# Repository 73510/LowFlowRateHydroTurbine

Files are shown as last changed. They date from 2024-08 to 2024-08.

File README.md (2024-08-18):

# LowFlowHydroTurbine 🌊⚡

이 저장소는 저유속 수차 연구와 관련된 두 개의 주요 프로젝트를 포함하고 있습니다:

1. [한화 사이언스 챌린지 프로젝트: 저유속 접이식 날개 수차](./HSC2023%20한화%20사이언스%20챌린지/)
2. [KSEF (Korea Science & Engineering Fair) 저유속 수차 연구 프로젝트](./KSEF/)

## 프로젝트 개요 🔍

### 1. 한화 사이언스 챌린지 프로젝트 🏆

이 프로젝트는 저유속 환경에서 효율적으로 작동하는 접이식 날개 수차를 개발하는 것을 목표로 합니다.

주요 구성 요소:
- CFD 분석 데이터 & 코드 💻
  - [CFD automation을 통한 시뮬레이션 과정 효율화](./HSC2023%20한화%20사이언스%20챌린지/Analysis%20Data%20and%20Code/Code%20and%20DXF/CFD%20automation/)
  - [CFD 분석 결과를 통한 토크 최대화](./HSC2023%20한화%20사이언스%20챌린지/Analysis%20Data%20and%20Code/Code%20and%20DXF/Optimize_dxfV1.ipynb)
- 아두이노 코드 🤖
- 설계 파일 (3D 모델링, STL) 🖨️
- 제출 자료 및 문서 📊

[자세한 내용 보기](./HSC2023%20한화%20사이언스%20챌린지/README.md)

### 2. KSEF 저유속 수차 연구 프로젝트 🔬

이 프로젝트는 한화 사이언스 챌린지에서 진행한 연구를 발전시켜 KSEF에 출품한 것입니다.

주요 구성 요소:
- 빌드 파일 (BUILD) 🏗️
- 코드 분석 (Code Analysis) 📊
- 치수 설계 (DIMENSION) 📏
- 문서 (Documentation) 📚

[자세한 내용 보기](./KSEF/README.md)

## 저장소 구조 📂

```
LowFlowHydroTurbine/
├── HSC2023 한화 사이언스 챌린지/
│   ├── Analysis Data and Code/
│   ├── Arduino/
│   ├── 설계/
|   ├── Media/
│   └── 한화 사이언스 챌린지 제출 자료/
└── KSEF/
    ├── BUILD/
    ├── Code Analysis/
    ├── DIMENSION/
    ├── Media/
    └── Documentation/
```

## 주요 기능 및 특징 🌟

- 저유속 환경에 최적화된 수차 설계
- CFD (Computational Fluid Dynamics) 분석을 통한 성능 최적화
- 아두이노를 이용한 실험 환경 제어 및 데이터 수집
- 3D 모델링 및 프로토타입 제작
- 다양한 설계 반복을 통한 성능 개선

## 연구 결과 📈

### 한화 사이언스 챌린지 대상
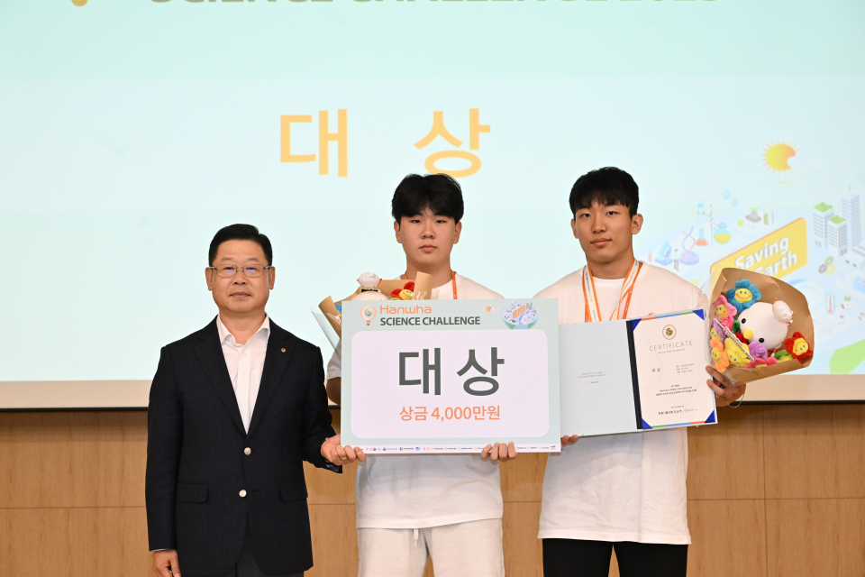
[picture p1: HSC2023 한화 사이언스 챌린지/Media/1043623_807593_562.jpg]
  

  

### KSEF 은상
  
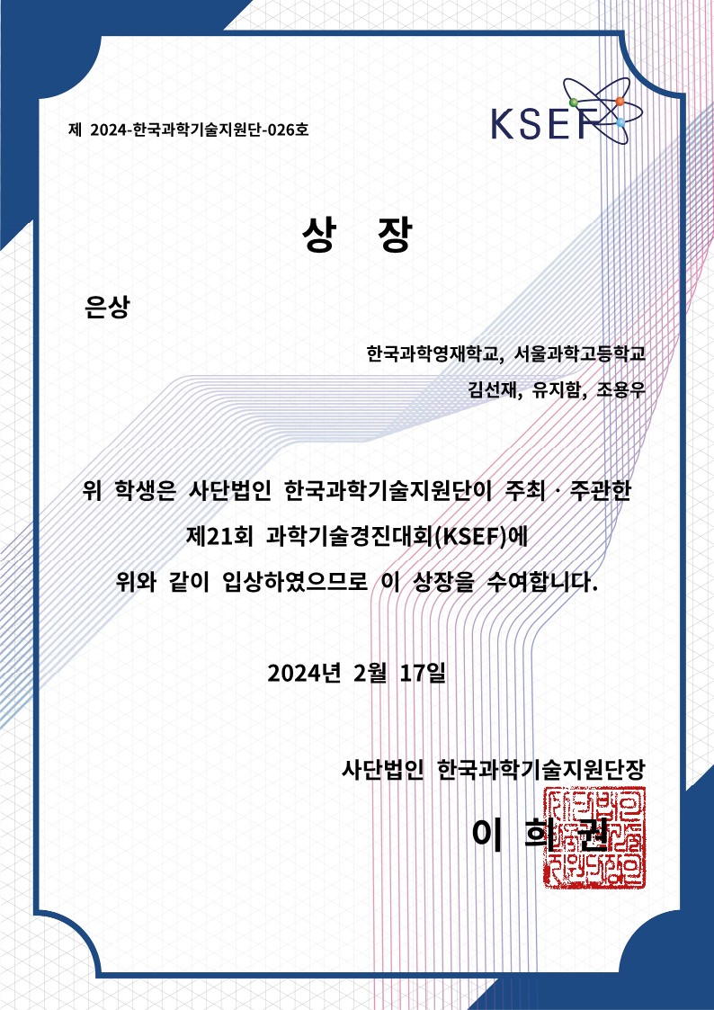
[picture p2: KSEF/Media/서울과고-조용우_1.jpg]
 

 

### 데이터 분석 결과
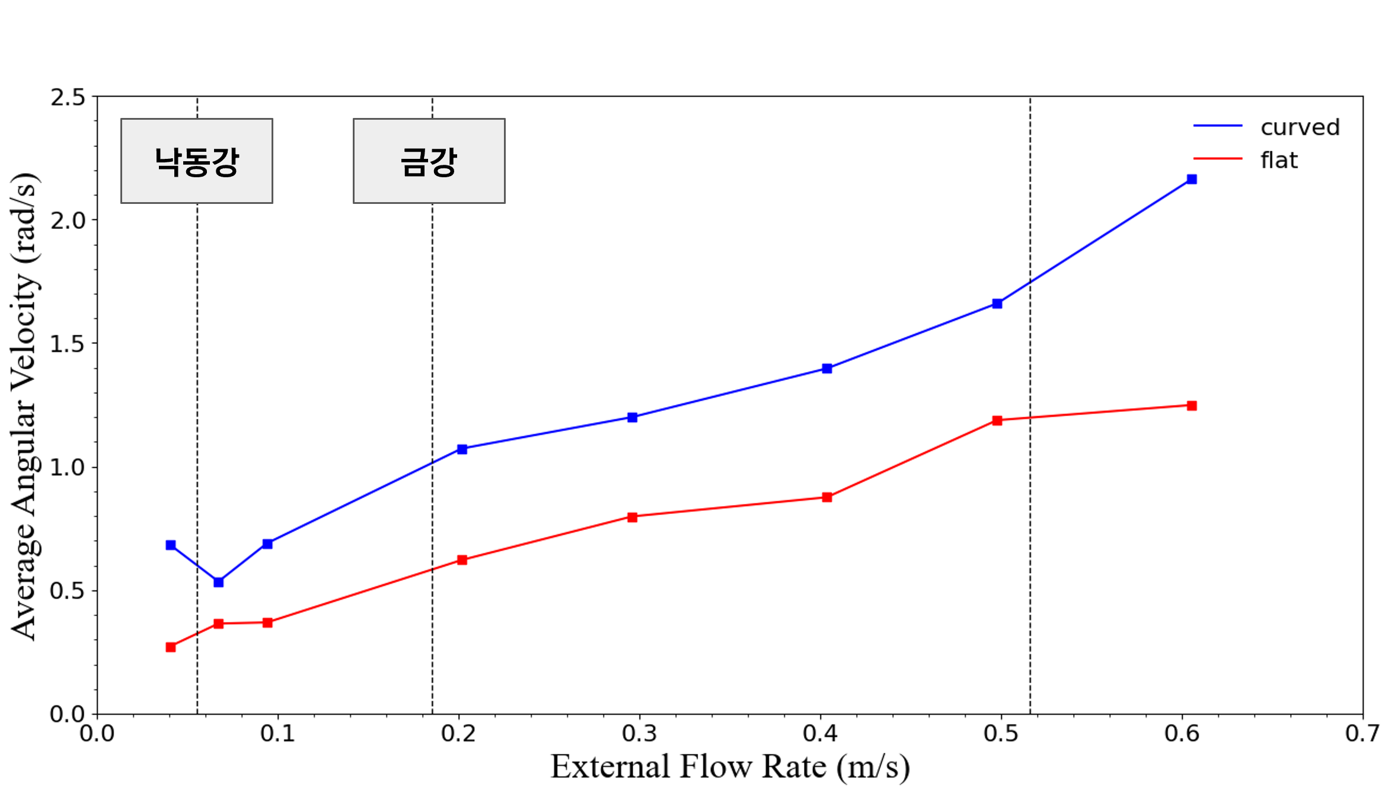
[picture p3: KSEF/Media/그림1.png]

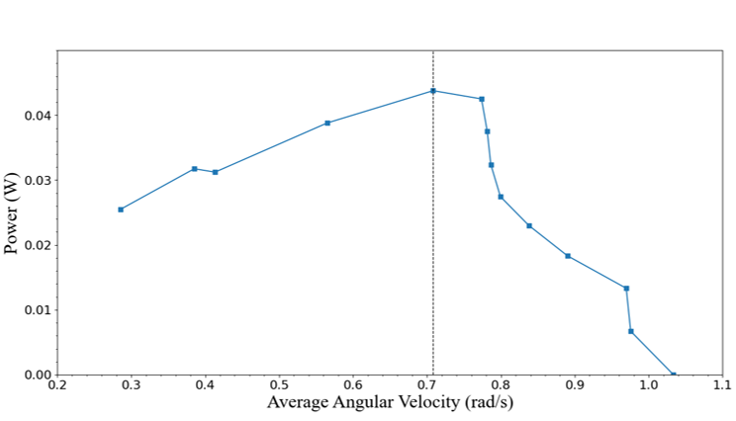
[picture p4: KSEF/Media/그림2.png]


## 기여 및 문의 💌

이 프로젝트에 관심이 있거나 기여하고 싶으신 분들은 언제든지 연락 주시기 바랍니다. 질문이나 제안사항이 있으시면 이슈를 생성하거나 pull request를 보내주세요.

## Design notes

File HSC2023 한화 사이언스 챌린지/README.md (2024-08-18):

# LowFlowHydroTurbine
# 한화 사이언스 챌린지 프로젝트: 저유속 접이식 날개 수차

이 저장소는 한화 사이언스 챌린지에 출품한 저유속 접이식 날개 수차 프로젝트의 모든 자료를 포함하고 있습니다.

## 목차

1. [CFD 분석 데이터 (CFD Analysis Data)](#분석-데이터)
2. [아두이노 코드 (Arduino)](#아두이노-코드)
3. [설계 파일 (Design Files)](#설계-파일)
4. [한화 사이언스 챌린지 제출 자료 (Files submitted to Hanwha Science Challenge)](#한화-사이언스-챌린지-제출-자료)

## [CFD 분석 데이터](./Analysis%20Data%20and%20Code/)

Computational Fluid Dynamics (CFD) 분석 및 최적화 관련 파일들이 이 섹션에 포함되어 있습니다.
[**Code and DXF**](./Analysis%20Data%20and%20Code/Code%20and%20DXF/)
- optimize_dxfV1
  - 수차의 CFD 결과 기반 토크 계산 및 최적화
  - 최적화 이후 Smoothing 코드
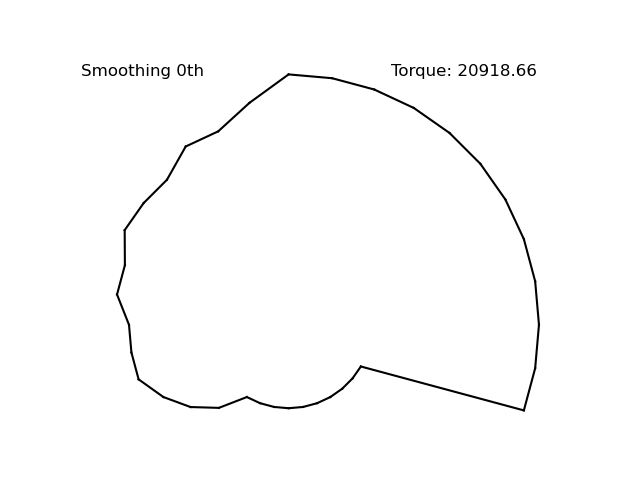
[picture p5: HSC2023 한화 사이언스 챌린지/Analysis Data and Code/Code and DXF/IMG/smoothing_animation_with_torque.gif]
  
  - 분석 기반 DXF (Angleblock 단면 형상) 제작 코드
- full, half, straight, straightWF : 각 날개의 최적화 DXF 형상

- [**CFD automation**](./Analysis%20Data%20and%20Code/Code%20and%20DXF/CFD%20automation/)
  - 0~360도까지, 10도 단위로 유속과 날개가 이루는 각을 바꾸어가며 날개가 받는 힘을 측정하는 코드. 
  - 이 과정에서, 반복되는 작업을 pyautogui로 자동화하여 효율화시켰습니다.
  - [fullauto.py](./Analysis%20Data%20and%20Code/Code%20and%20DXF/CFD%20automation/fullauto.py) : 완전히 자동화 시켜 0~360도까지 반복하며 데이터를 기록
  - 이로써 36*4 = 144개의 CFD 데이터를 일관되게 얻었습니다.
  - 작동 영상

코드 실행부터 CFD 실행까지



CFD 실행 이후, 벽 계산기로 토크를 계산하는 과정 자동화



## [아두이노 코드](./Arduino/)

실험 환경 제어 및 데이터 수집을 위한 아두이노 코드가 이 섹션에 있습니다.
- [어항 내 물의 흐름을 제어하는 코드 (단순 속도)](./Arduino/Motor_Control_SpeedControlOnly)
- [어항 내 물의 흐름을 제어하며 유속과 수차의 회전 속도를 IR 센서로 측정하는 코드](./Arduino/Motor_Control_SpeedControlandTachometer)

## [설계 파일](./설계/)

수차와 관련 부품들의 3D 모델링 파일 및 설계도면이 이 섹션에 있습니다.

- [STL](./설계/STL/) : 수차를 설계한 STL 파일을 모았습니다.
- [어항 설계](./설계/어항%20설계/) : 어항 구조물을 설치하는데 사용한 설계 파일입니다.
- Acryl Wall Arduino Placement : 아두이노를 설치하기 위해 만든 아크릴 판 구조물입니다.
- Acryl Wall : 아크릴 벽으로 어항 내부의 흐름을 나누어 순환하게 했습니다.

## [한화 사이언스 챌린지 제출 자료](./한화%20사이언스%20챌린지%20제출%20자료/)

프로젝트 관련 모든 문서 파일들이 이 섹션에 포함되어 있습니다:

- 아이디어 발표 자료
- 토론 발표 자료
- 한사챌 보고서
- 기존 연구 결과 자료
- 결과 전시물 계획서
- 판넬사진 출력 파일
- 기존 연구 특허출원번호 10-2010-0027024 수정 날개 접이식 수차 자료

이 문서들은 프로젝트의 전체적인 진행 과정, 연구 결과, 및 최종 제출 자료들을 포함하고 있습니다.

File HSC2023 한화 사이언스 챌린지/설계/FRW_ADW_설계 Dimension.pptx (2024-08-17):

## HSC2023 피쉬파워

## 설계 Dimesion Documentation

- 회전부는 0.7mm 여분 (지름기준), 고정부는 0.2mm 여분 (지름 기준)
- -> 이거 한번 싹다 검토하고 맞추기

## 베어링이 필요한가?

- 추가적인 무게
- 감소하는 저항
- 증가하는 안정성
- 불필요한 이동의 제한
- 부품 수의 증가, 조립 시간 길어짐, 파손 우려 높아짐

## 어떤 봉을 쓸 것인가

6mm환봉
6mm 4mm 파이프는 파손될 우려가 있어 약간 보강한다.

## 어항

- 일단 어항 자체는 측정이 필요.
사용 어항 링크 (https://www.coupang.com/vp/products/4395243507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)

## 어항 profile & 실험장치

Aluminum Profile 20 * 20 필요한 것 :
424 * 3
110 * 2
100 * 1
585 * 2
290 * 3
145 * 1
이거만 있으면 됨.

3D printed parts :
3D motor mount
Barmount 0,1
Barmount 3

## 어항 profile 실험장치의 주요 settings

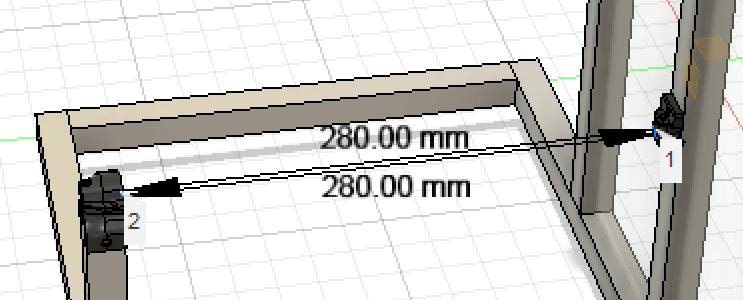
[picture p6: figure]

RotorBar Length : 290

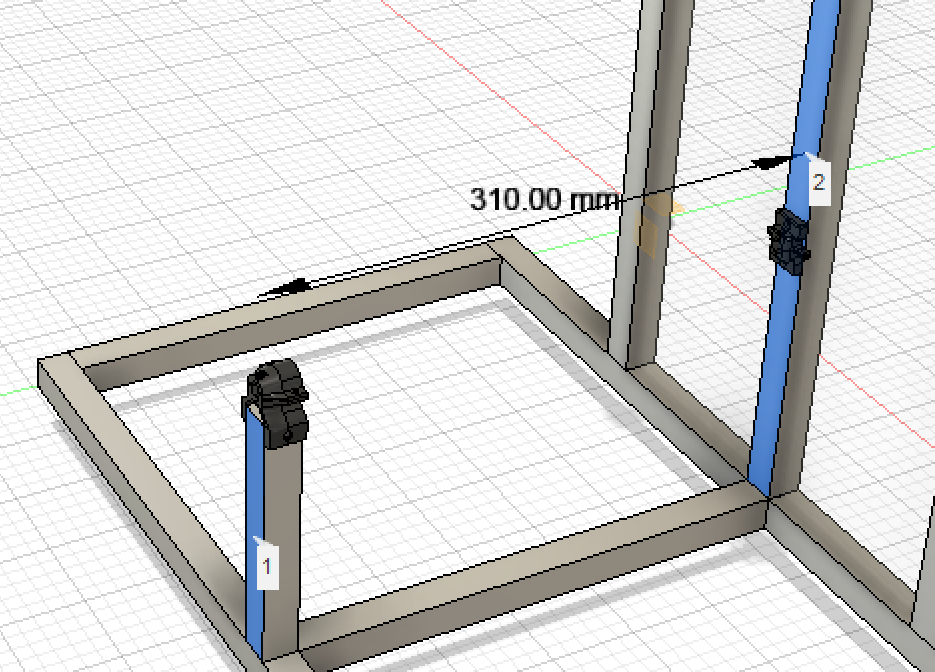
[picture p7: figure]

Rotor Parts Length : 290-30 = 260mm
Barmount 01이 10mm
Barmount 3이 20mm 먹음
둘 다 끝단에서 5mm 떨어진 중심에서 3mm 빵꾸 내놓음.
필요 고정 나사 : 16~20mm
RotorBar는 고정되어있음.

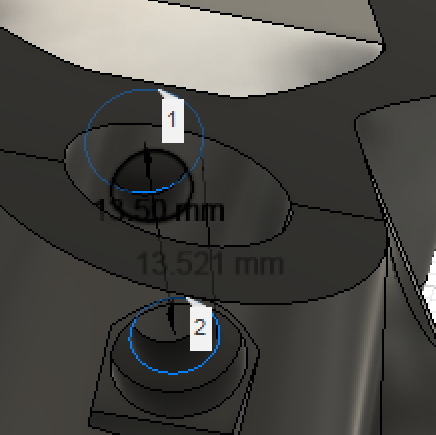
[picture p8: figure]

## 자유회전 물레방아 (FRW)

- Free Rotating Wheel

## FRW, 축 정의

B center rotational axis / B 중심 회전축 -> B-CRA

B Flap rotational axis / B 날개 회전축 -> B-FRA

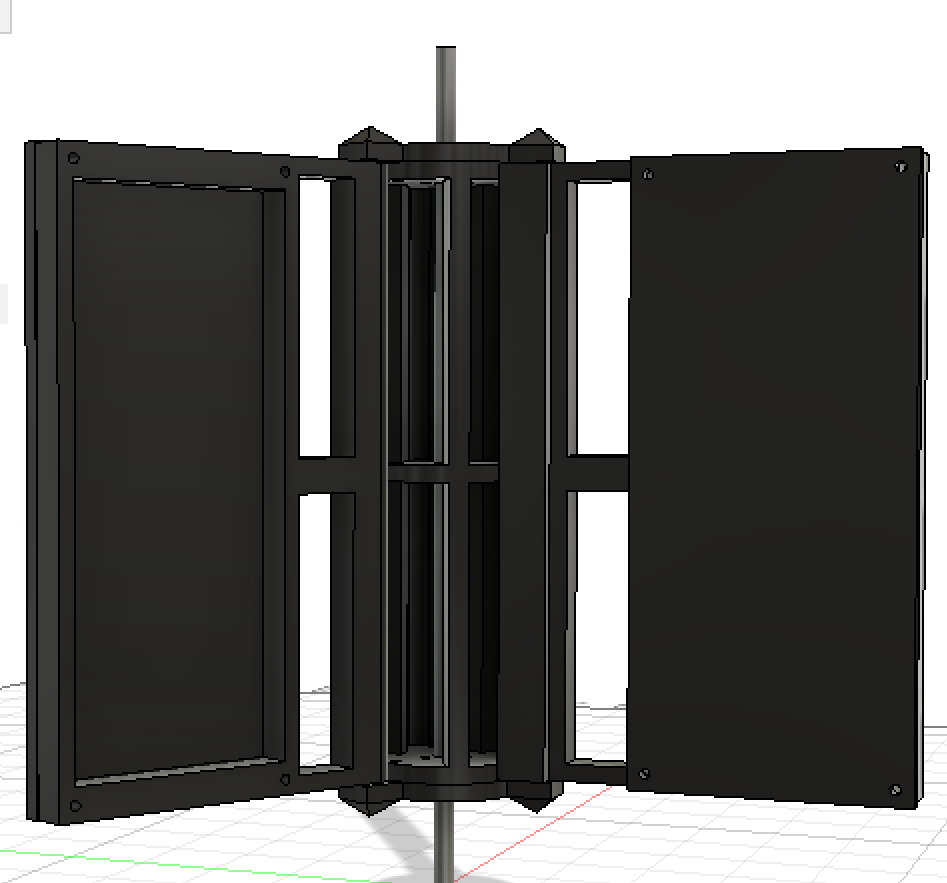
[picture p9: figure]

B : Bar

## FRW : Axial dimesion

gearAT : axial thickness of gear 기어의 축방향 두께
FlapcapAT : axial thickness of gear / Flapcap의 축방향 두께
FlapAT : axial thickness of flap / Flap의 축방향 두께
S1 : space between flapcap(L, R) and flap / flapcap 과 flap 사이의 여분 공간
CenterPieceAT : axial thickness of CenterPiece / CenterPiece 의 축방향 두께
S2 : space between gear and barmount / gear와 barmount 사이의 두께
S3 : space between FlapcapR & barmount
Black : Rotating Parts, Drilled on to B-CRA (rotates with B-CRA)
Blue : not rotating Parts, connected to B-CRA via Bearing
S : spaces (needs to be bigger than 1mm)

Barmount
01

S2

gearAT

flapcapAT
(L)

S1

FlapAT

CenterPieceAT

S1

flapcapAT
(R)

S3

Barmount
3

## FRW Radial Dimension

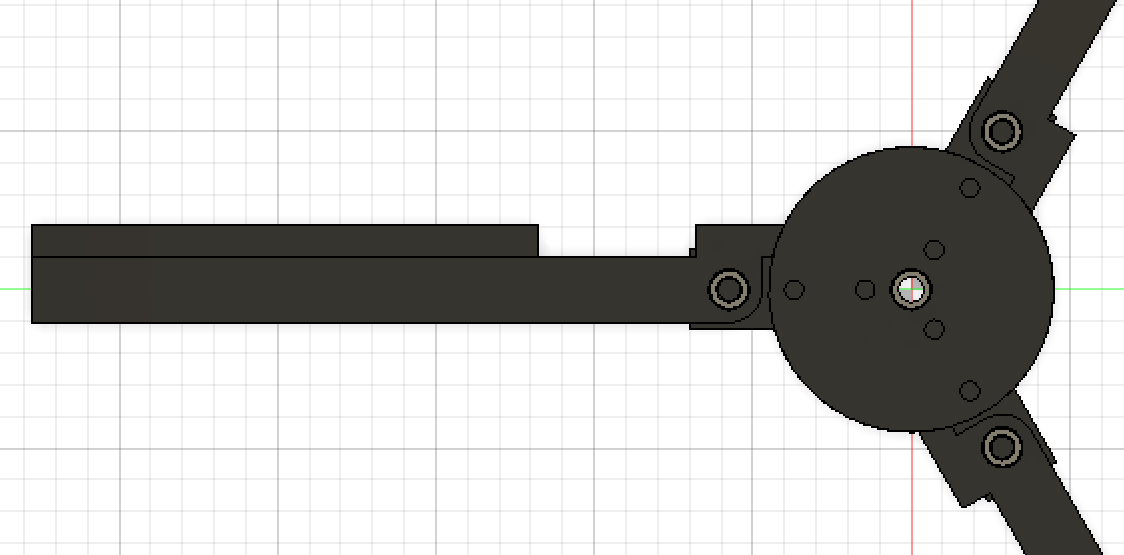
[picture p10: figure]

FF-RT = 90
(Flap Frame Radial Thickness)

F-RT = 80
(Flap Radial Thickness)

B-CRA to B-FRA = 60

## FRW – constraints for build

Barmount
01

S2

gearAT

flapcapAT
(L)

S1

FlapAT

CenterPieceAT

S1

flapcapAT
(R)

S3

Barmount
3

s2+ gearAT + 2*flapcapAT + CenterPieceAT + s3 = 280mm
2s1 + flapAT = CenterPieceAT
gearAT >= 10, flapcapAT >=10
S >=2
+ flapAT = flapAT(camversion, cyclodialversion)

## FRW – Axial/Radial 수치

Axial 수치
gearAT = 16mm
Total -> 2*2 + 16 + 10*2 + 124 = 164mm
중심에서 24mm 떨어뜨려서 배치필요.

Radial 수치
FF-RT = 90
F-RT = 80
B-CRA to B-FRA = 60
G to FC mount = 10
FC to CB mount = 40
CB roller = 50

## ADW/ 각도 정의 물레방아

- Angle Defined 물레방아

## ADW, 축 정의

B center rotational axis / B 중심 회전축 -> B-CRA

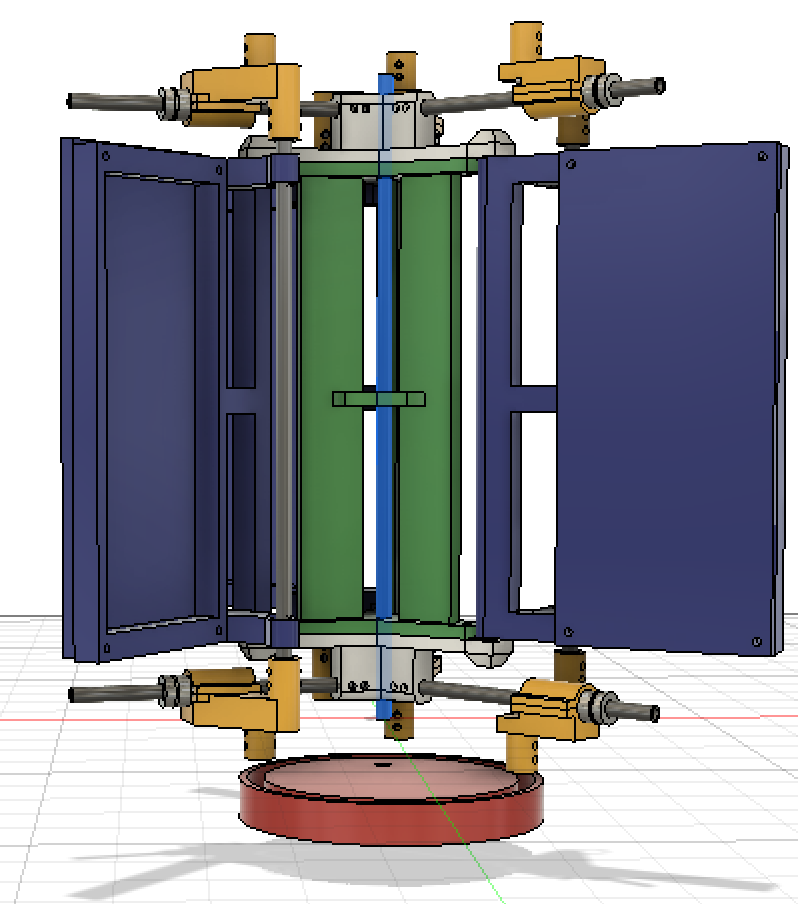
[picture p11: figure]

B Flap rotational axis / B 날개 회전축 -> B-FRA

B Flap pin slot/ B 날개 각도축 -> B-FPS

B Angle Linear Axis / B 각도선형축 -> B-ALA

B Angle rod -> B-AR

B : Bar

## ADW 부품 정의

CB - CenterBody / 중심체

FF - Flap frame / 날개 뼈대

F - Flap / 날개

FC - FlapCap / 날개 뚜껑

LAG - Linear Angle guide / 선형 캠 가이드

AB - AngleBlock / 각도블럭

## ADW LAG (linear angle guide) dimension

1. Tangent to radial vector

B-FPS fix

LAG main body / LAG-MB

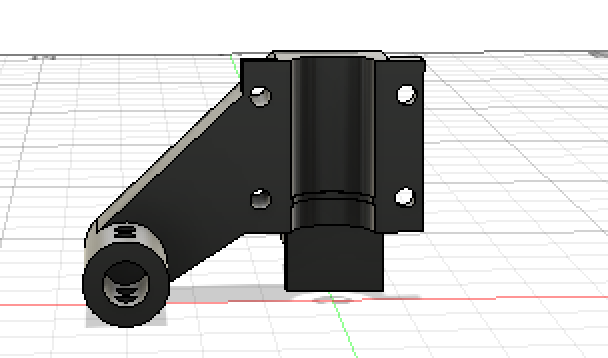
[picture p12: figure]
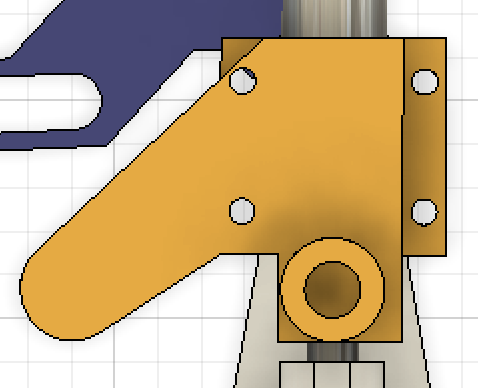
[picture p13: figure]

B-AR fix

LAG leftover

Δy

LAG bearing holder / LAG_BH

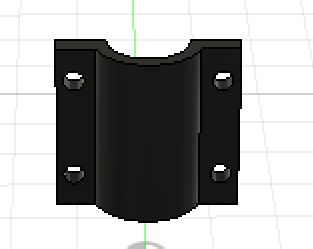
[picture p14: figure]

d

현재 설계에서 d = 30mm, Δy = 0mm

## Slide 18

ADW LAG_L (linear angle guide) dimension

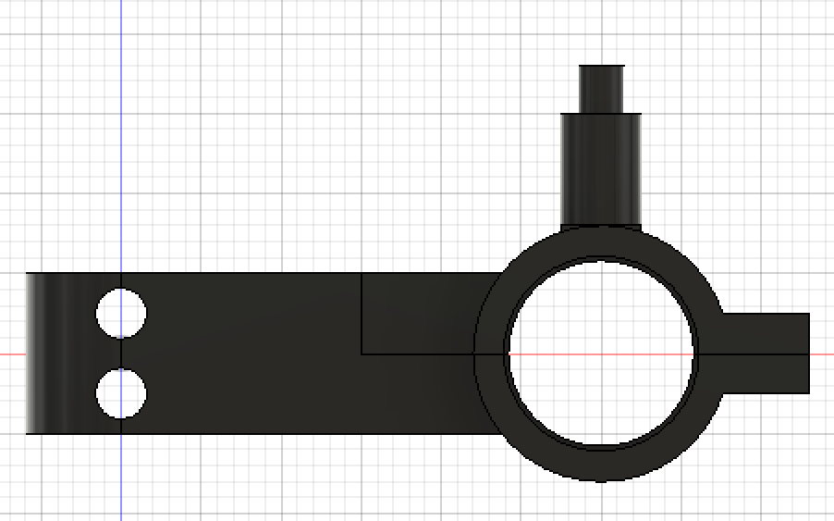
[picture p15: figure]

BFL : Bar Fix Length
FT : FixingThickness
LAG-B-AT : LAG Body Axial thickness
Bearing Diameter = 12mm
B-ALA to BearingMount = 15mm
Bearing type = 683zz

FT

BFL

## ADW LAG

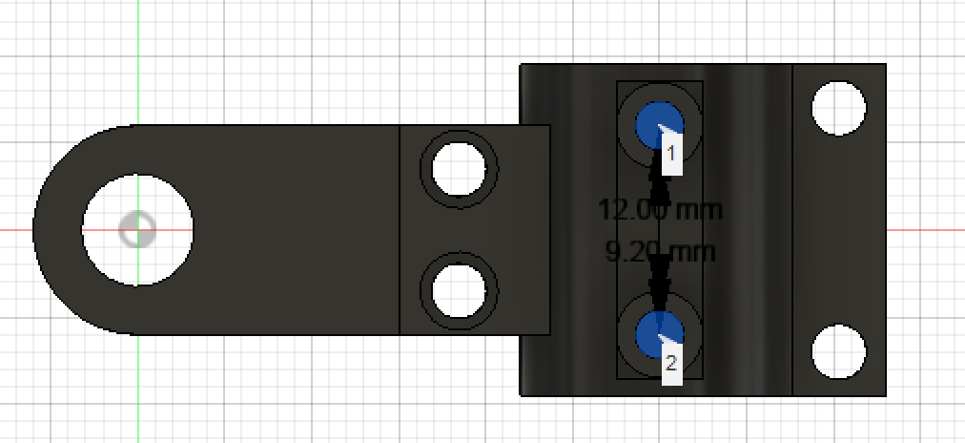
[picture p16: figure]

Angle Block 두께

distance of bearings (center) = 12mm
Bearing radius : 3.5mm
AB 두께 : 5mm, 여분 고려하여 4.5mm로 함. 별도의 베어링 고정은 없으며 필요시 글루건/순접으로 할 것

## ADW LAG dimensions

BFL : 10mm
FT : 1.8mm
LAG-B-AT : LAG Body Axial thickness
Bearing Diameter = 12mm
베어링 고정부 Diameter = (실제 고정시 편의를 위해 여분) ->6.1*2

## ADW Flapcap dimension

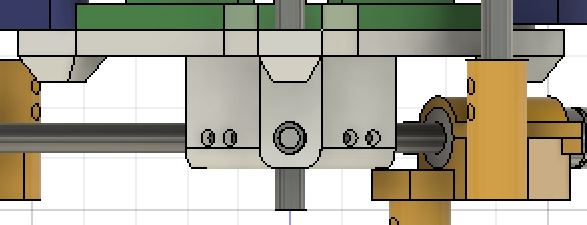
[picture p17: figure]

B-ALA-S : B-ALA spacing

Bar Margin

## ADW Axial Dimension

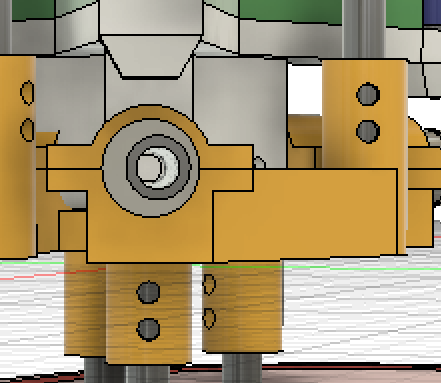
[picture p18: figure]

AB-AT : Angle Block Axial Thickness, 각도블럭 axial 두께
FC-AT : Flap Cap Axial Thickness, flapcap 축방향 두께
G-AT : Gear Axial Thickness, 기어 축방향두께
LAG-AT : Linear Angle Guide Axial Thickness
BFL : Bar Fix Length
LBT : Linear Bush Thickness
LAG-LB-B-T : LAG linear bearing body thickness
LAG-B-AT : LAG Body Axial thickness

Barmount
01

S

G-AT

S

AB-AT

S

BFL

LAG-B-AT

BFL

LAG-BH-AT

S1

FlapAT

CenterPieceAT

S1

BFL

LAG-BH-AT

LAG-B-AT

BFL

S

AB-AT

S

Barmount
3

B-ALA-S

B-ALA-S

## ADW

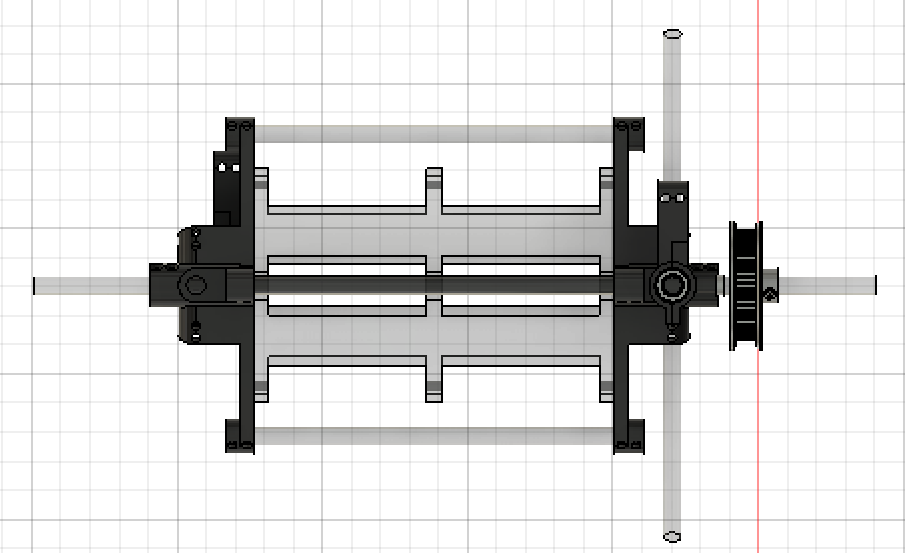
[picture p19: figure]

## ADW Radial Dimension

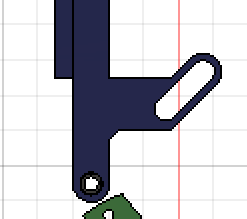
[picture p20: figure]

B-CRA to B-FRA

(2)^0.5 *d

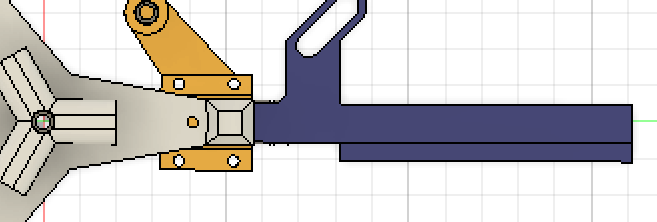
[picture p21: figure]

d

F-RT (Flap Radial Thickness)

B-ALA Fix

## ADW 0~90이 나오기 위한 Angle Block

When 45deg Flap Attached, Radial Value of Angle Block

0deg = (B-CRA to B-FRA) – d + Δy = 60-30 = 30
LAG는 중심에서 10정도 떨어져 있음
Bar Fix는 중심에서 20까지만 있어야 함.
90deg = (B-CRA to B-FRA) + d + Δy = 60+30 = 90
B-ALA 는 20~ 100까지 필요.
따라서 필요길이는 80, 고정부 15로 계산하여 길이 95임

## Constraints of ADW

Barmount
01

S

G-AT

S

AB-AT

S

BFL

LAG-B-AT

BFL

LAG-BH-AT

S1

FlapAT

CenterPieceAT

S1

BFL

LAG-BH-AT

LAG-B-AT

BFL

S

AB-AT

S

Barmount
3

B-ALA-S

B-ALA-S

5*S + G-AT + 2*(AB-AT + BFL + LAG-B-AT + B-ALA-S) + CenterPieceAT <= 280mm
S >= 2mm
2*S + FlapAT = CenterPieceAT
(B-CRA to B-FRA) – d - LAG leftover >= B-ALA Fix
(B-CRA to B-FRA) + F-RT <= 150
FlapAT (ADW, FRW, CPW)

## ADW parametrics

Axial 수치
S = 2
gearAT = 16mm
flapcap = 36mm
Flap = 120
CenterPieceAT = 124
BFL = 10
LAB-B-AT = 5
B-ALA-S = 10

LAG 수치
D = 30
Δy = 0 (하지만 d를 늘릴경우 증가 시켜야 함)

Radial 수치
FF-RT = 90
F-RT = 80
B-CRA to B-FRA = 60
G to FC mount = 10
FC to CB mount = 40
CB roller = 50

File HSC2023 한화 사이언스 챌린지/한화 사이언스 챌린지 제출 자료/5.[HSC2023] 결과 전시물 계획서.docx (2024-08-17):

전시 결과물 계획서

[계획서 작성 안내]

- 조형물의 규격 및 특이사항을 명기하고, 사진자료를 첨부하여 1매 이내로 작성하여, 타 연구자료와 함께 제출하여 주시기 바랍니다.

- 운영위원회 결정에 따라 결과물 전시가 제한될 수 있습니다.
(안전, 위험성 등 고려)

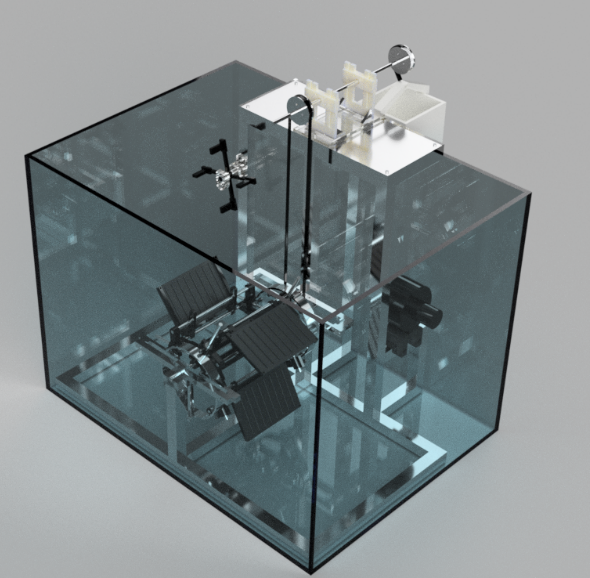
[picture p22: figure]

60 x 45 x 45cm 어항 + 실험장치입니다. 물을 넣어야 해서 바퀴 달린 수레 위에 올려놓고 사용하고자 합니다. 저희 집에서 사용할 정도로 안전합니다.

수레 위에 올려놓고 사용하면 130 * 80 * 80 cm 일 것으로 예상됩니다.

프로젝트명 | 저유속에서 발전가능한 접이식 날개 수차
팀명 | 피쉬 파워
지도교사 성명 | 배동일
팀원 성명 | 1. 조용우 | 2. 서동주

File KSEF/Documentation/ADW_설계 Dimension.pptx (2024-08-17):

## ISEF_ADW

## 베어링이 필요한가?

베어링 종류 – 682OP
외경 5, 내경 2, 두께 1.5
ADW FF에는 베어링 없이 함.

## 어떤 봉을 쓸 것인가

외경6mm 내경 4mm 파이프
2mm 카본 로드

## ADW, 축 정의

B center rotational axis / B 중심 회전축 -> B-CRA


B Flap rotational axis / B 날개 회전축 -> B-FRA

B Flap pin slot/ B 날개 각도축 -> B-FPS

B Angle Linear Axis / B 각도선형축 -> B-ALA

B Angle rod -> B-AR

B : Bar

## ADW 부품 정의

CB - CenterBody / 중심체

FF - Flap frame / 날개 뼈대

F - Flap / 날개

FC - FlapCap / 날개 뚜껑

LAG - Linear Angle guide / 선형 캠 가이드

AB - AngleBlock / 각도블럭

## ADW Axial Dimension


AB-AT : Angle Block Axial Thickness, 각도블럭 axial 두께
FC-AT : Flap Cap Axial Thickness, flapcap 축방향 두께
G-AT : Gear Axial Thickness, 기어 축방향두께
LAG-AT : Linear Angle Guide Axial Thickness
BFL : Bar Fix Length
LBT : Linear Bush Thickness
LAG-LB-B-T : LAG linear bearing body thickness
LAG-B-AT : LAG Body Axial thickness

Barmount
01

S

G-AT

S

AB-AT

Linear Bearing Casing Diameter

FlapCap

FlapCap

Linear Bearing Casing Diameter

AB-AT

Barmount
3

LAGAB

Til B-ALA

B-ALA-S

S1

FlapAT

CenterPieceAT

S1

Til B-ALA

B-ALA-S

## ADW Radial Dimension


B-CRA to B-FRA

(2)^0.5 *d


d

F-RT (Flap Radial Thickness)

B-ALA Fix

## Constraints of ADW

G-AT

Barmount
01

AB-AT

Linear Bearing Casing Diameter

FlapCap

FlapCap

Linear Bearing Casing Diameter

AB-AT

Barmount
3

LAGAB

Linear Bearing Casing Diameter

B-ALA-S

S1

FlapAT

CenterPieceAT

S1

B-ALA-S

Barmount01 10mm
S = 2
G-AT = 10
AB-AT = 20
LAGAB_ = 20
Linear Bearing Casing Diameter = 8
B-ALA-S = 10
FlapCap = 5

S

S

S

Linear Bearing Casing Diameter

## ADW parametrics

Axial 수치
Barmount01 10mm
S = 2
G-AT = 10
AB-AT = 20
LAGAB_ = 20
Linear Bearing Casing Diameter = 8
B-ALA-S = 10
FlapCap = 5

LAG 수치
D = 20
Δy = 19/2 (하지만 d를 늘릴경우 증가 시켜야 함)

Radial 수치
FF-RT = 50
F-RT = 45
B-CRA to B-FRA = 40
40+20+19/2+20 = 90
110-8

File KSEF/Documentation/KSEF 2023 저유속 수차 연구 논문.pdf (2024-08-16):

제21회 KSEF과학프로젝트대회

- 1 -

### 1. Introduction

친환경적이면서 동시에 유의미한 발전을 할 수 있는 에너지 하베스팅 방식은 흔하지 않다. 현존하는 수력 발전 시스템은 빠 른 유속을 요구하거나, 큰 수위 차를 요구하는데, 해당 두 조건 이 만족되지 않는 환경에서는 인위적으로 댐을 설치하여 수력 발전을 가능케 하기도 한다. 이러한 기존 수력 발전 시스템은 환경적인 면에서 좋지 않다는 평가를 받고 있다.
물레방아는 댐과 같은 수력 발전 방식과 비교했을 때 24시간 발전이 가능하고, 비교적 친환경적이라는 큰 장점을 가지고 있 다. 다만 기존의 물레방아는 그 구조와 관계없이, 반드시 일부 분이 물에 잠겨야만 한다는 단점을 지니고 있다. 그림 1에 나 타난 대표적인 형태의 물레방아들 모두 물의 흐름이 균일할 때 일부분이 잠겨서 토크를 얻는 방식을 이용하고 있다.

[Fig. 1] 물레방아의 회전 원리, 왼쪽부터 Undershot water wheel, applied for watermilling since the 1st century BC / Overshot water wheel, applied for watermilling since the 1st century BC / Breastshot water wheel, applied for watermilling since the 3rd century AD

따라서 기존의 물레방아는, 물레방아가 물에 전부 다 잠긴 상 황에서는 돌림힘이 작용하지 않아 에너지를 생산할 수 없다는 큰 단점을 지닌다. 이는 물레방아의 설치를 어렵게 하고, 환경 적 변수가 발생했을 시 수선이 까다로우며, 조경을 해치는 원인 이 된다. 본 연구에서는 물레방아에 캠 구조와 수동적 날개 조 정 시스템을 적용해, 물에 전부 다 잠긴 상태에서도 에너지 생

## 수동적 날개 조정을 위한 캠 구조 적용 수중 물레방아의 설계 및 제작

김선재¹

, 유지함¹

, 조용우²
1한국과학기술원 부설 한국과학영재학교,

2서울과학고등학교

## Design and Development of an Underwater Watermill with Cam Orientation for Passive Blade Pitching System

Sunjae Kim¹

, Jihahm Yoo¹

, Yongwoo Cho²
1Korea Science Academy of KAIST, Busan, Korea 2Seoul Science High School, Seoul, Korea

요 약 캠 구조와 수동적 날개 조정 시스템을 이용한 물레방아는 물 안에 전부 잠겨도 돌림힘이 작용해 에너지를 생산할 수 있다. 본 연구에서는 캠 구조와 수동적 날개 조정 시스템이 적용된 물레방아의 에너지 생산량과 기존 방식 대비의 환경적 이득을 탐구하였다. 먼저 간단화 시뮬레이션을 통해 본 연구의 물레방아가 수중에서 회전할 수 있음을 검증하였고, Fusion 360 프로그램을 통해 모델링하였다. 이후 초기 버전으로 3-Flat Version을 제 작한 후, 날개 수와 날개 모양을 수정해 최종적으로 4-Flat Version과 4-Curved Version의 두 물레방아를 제작하였다. 제작된 두 물레방아를 Endless Pool과 직접 제작한 실험 환경에서 실험해 외부 유속 vs. 평균 각속도 vs. Power 데이터를 획득한 결과, 본 연구의 물레방아가 기존 물레방 아가 발전하지 못하던 환경에서도 큰 수준의 에너지를 생산할 수 있음을 확인할 수 있었으며, 현재 수중 에너지 발전 방식으로 많이 이용되고 있는 Underwater Windmill과 비교해도, 본 연구의 물레방아가 환경적인 측면에서 큰 이점을 가짐을 검증하였다. 향후 연구에서 본 장치의 마찰 최소화(자 기 부상), 캠 구조의 개선, 그리고 대형화를 통해 본 연구의 물레방아의 발전량을 유의미하게 증가시킬 수 있을 것으로 기대한다.

Abstract The waterwheel equipped with a cam structure and a passive wing adjustment system can produce energy even when fully submerged in water due to the action of rotational force. In this study, the energy production of the waterwheel equipped with the cam structure and passive wing adjustment system was investigated, along with the environmental benefits compared to conventional methods. Initially, the waterwheel's ability to rotate underwater was verified through simplified simulations, and the model was designed using Fusion 360 software. Subsequently, an initial version, the 3-Flat Version, was fabricated and further modified in terms of the number and shape of the wings. Finally, two waterwheel versions, the 4-Flat Version and the 4-Curved Version, were produced. Experiments were conducted using the fabricated waterwheels in an Endless Pool and a testbed constructed at the school to acquire data on external flow rate vs. average angular velocity vs. power. The results revealed that the waterwheel in this study could produce a substantial amount of energy even in environments where conventional waterwheels could not, and when compared to the widely used underwater windmill for underwater energy generation, it exhibited significant environmental advantages. Future research is expected to focus on minimizing friction (magnetic levitation), improving the cam structure, and scaling up the device, aiming to significantly increase the waterwheel's power generation capacity. Key Words : Underwater Watermill, Cam, Passive Blade Pitching System, Energy Harvesting

- 2 -

산을 가능하게 하여 기존 물레방아의 단점을 해결하고, 친환경 적이면서 효과적인 수중 에너지 발전 방식을 제시하고자 한다.

### 2. Background Study

2.1 기존 접이식 날개를 이용한 수력 발전 모델

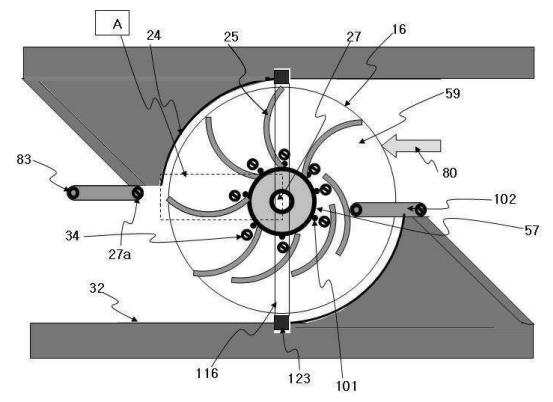
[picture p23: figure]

[Fig. 2] 대한민국 특허청에 등록된 특허 10-2010-0027024, 접이식 날개 수차

위의 접이식 날개를 이용한 수력 발전 모델은 유도판 을 사용하여 날개를 접어 토크의 차이를 발생시켜 발전 을 하는 방식이다. 해당 모델은 날개들이 유도판에 충 돌을 하면서 날개가 접히는 방식으로 설계를 하였다. 양쪽에 설치된 유도판은 복류식으로 발전이 가능하도록 설계되었고, 저 유속, 저 낙차에서도 높은 효율로 발전 할 수 있도록 설계되었다.

2.2 펠톤 터빈

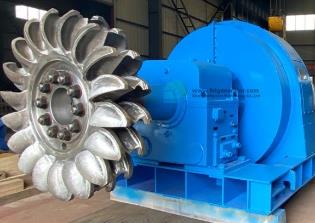
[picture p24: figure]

[Fig. 3] 펠톤 터빈

펠톤 터빈은 물을 노즐로부터 분출시켜 위치 에너지 를 운동에너지로 바꾸는 수차로 충돌형 수차이다. 수압 에 의해 버킷에 부딪히는 물의 힘으로 회전력을 발생시 킨다. 유량을 조정할 수 있는 기구를 갖추고 있고, 유량 조정이 최우선 되는 경우에 사용할 수 있다. 펠톤 수차 는 단류식 수차이다.

2.3 캠 샤프트 구조(Cam Shaft Structure)

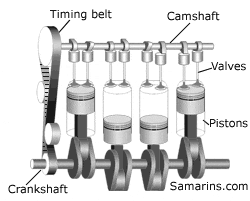
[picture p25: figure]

[Fig. 4] Cam Shaft 구조

캠 샤프트는 내부 연소 엔진의 작동을 제어하는 중요 한 부품 중 하나로, 밸브의 개방과 폐쇄를 조절하여 연 소 과정을 조절한다. 카메라 샤프트는 엔진 블록 내부 에 위치하며, 엔진의 크랭크 샤프트와 동기화하여 작동 한다.

캠 샤프트는 여러 개의 커브 또는 로브로 구성되어 있으며, 이 커브들은 밸브의 개방과 폐쇄 시기를 결정 한다. 엔진 작동 시, 크랭크 샤프트의 회전과 함께 카메 라 샤프트도 회전하게 되며, 각 로브의 모양과 크기에 따라 밸브가 열리고 닫히는 타이밍이 결정된다.

캠 샤프트는 크게 흡기 밸브와 배기 밸브의 작동을 제어하는 두 가지 유형으로 나뉜다. 인테이크 샤프트는 연료와 공기가 실린더 내부로 흡입되는 과정을 제어하 며, 익스테이크 샤프트는 연소 후 배기 가스가 실린더 에서 배출되는 과정을 제어한다.

2.4 수동적 날개 조정을 위한 캠 구조 적용 수중 물 레방아의 회전 원리

본 연구에서 제작한 수동적 날개 조정을 위한 캠 구 조 적용 수중 물레방아는 2.1의 접이식 날개와 2.3의 캠 샤프트 구조를 중심적으로 이용한다. 기울어진 날개 들을 통해 균일한 유속에서도 토크를 발생시키는 것이 본 연구의 물레방아의 기본 원리인데, 캠 구조를 통해 날개가 기울어지는 각도를 자유자재로 제어하여 이를 실현하였다.

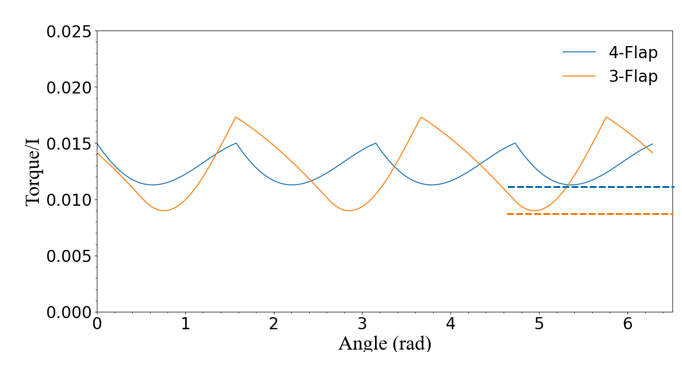
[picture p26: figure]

- 3 -

### 3. 간단화 시뮬레이션

3.1 토크 방정식 유도

본 절에서는 수동적 날개 조정을 위한 캠 구조 적용 수중 물레방아의 적용 가능성을 간단화 시뮬레이션을 통해 확인하고자 한다.

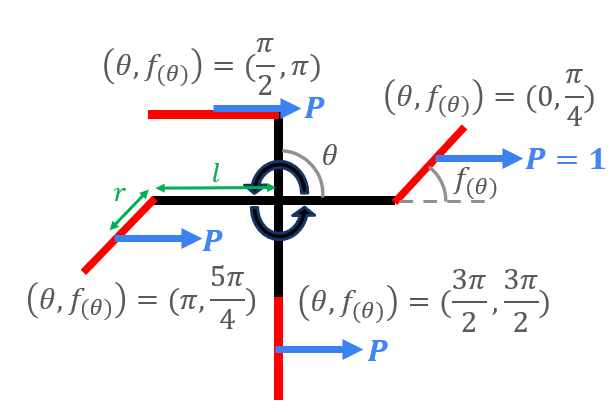
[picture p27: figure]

[Fig. 4] 간단화 시뮬레이션, 물레방아 구조와 상황

위 그림 4는 물이 왼쪽에서 오른쪽으로 흐르는 상황 에서의 물레방아 상황을 나타낸 그림이다. 원래 물의 흐름을 고려해 각 날개에 작용하는 힘의 크기를 구해야 하지만, 본 간단화 시뮬레이션에서는 각 날개에 크기 1 의 압력이 중심에 균일하게 작용한다고 가정한다. 이때 물레방아와 날개를 잇는 부분의 각도를 θ라 정의하고, 날개의 각도를 f(θ)라 정의하자. θ의 범위에 따른 f(θ)의 크기는 아래의 수식을 만족한다.

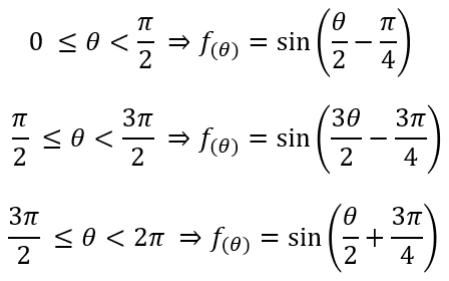
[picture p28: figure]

[Fig. 5] θ의 범위에 따른 f(θ)의 크기

따라서 날개의 개수가 4개인 상황에서 물레방아가 받 는 토크는 아래와 같다.

[Fig. 6] 유도된 토크 방정식

3.2 시뮬레이션 결과

그림 6의 토크 방정식을 그래프로 나타내면 아래와 같 다.


[Fig. 7] 한 바퀴 회전 동안 4-Flat 물레방아가 받는 토크

한 바퀴를 회전하는 동안 물레방아가 받는 토크의 방 향이 일정함을 그림 7을 통해 확인할 수 있다. 따라서 저항만 충분히 작다면, 본 연구의 물레방아는 충분히 회전할 수 있어서 에너지를 생산할 수 있음이 예측되었 다.

3.3 간단화 시뮬레이션을 통한 날개 수 최적화

이후 | 서술할 제작과정에서 | 우리는 먼저 3-Flat
Version을 제작하였다. 3-Flat Version의 경우 잘 회전 함을 확인하였으나, 날개 수가 3개인 것이 과연 최적인 지에 대한 의문이 들어 시뮬레이션을 통해 최적의 날개 수를 탐색하고자 하였다. 날개 수는 자리의 협소함 때 문에 5개 이상이 불가하여, 3개의 날개 수 혹은 4개의 날개 수 중 어느 것이 최적인지 결정하는 것이 중요하 였다.

그림 6과 같이 날개의 개수 3개인 상황에서 물레방아 가 받는 토크는 아래와 같다.

[Fig. 8] 날개가 3개인 경우에 유도된 토크 방정식

3-Flat Version의 물레방아와 4-Flat Version 물레방 아의 회전 관성 비는 약 3:4이다. 우리는 토크/회전 관 성의 크기를 통해 어떤 날개 수가 가장 최적인지 확인 하고자 하였다.

[Fig. 9] 3-Flap과 4-Flap의 Torque/I vs. Angle 그래프


- 4 -

시뮬레이션 결과 한 바퀴를 회전하면서 물레방아가 받 는 토크/회전 관성의 크기의 최솟값이 4-Flap Version 일 때 더 큼을 확인하였다.

물레방아는 한 바퀴를 회전하면서 각속도가 빠른 영역 을 지나기도 하고, 각속도가 작은 영역을 지나기도 한 다. 토크/회전 관성의 최솟값이 작다면, 물레방아가 각 속도가 작은 영역을 지날 때 멈출 가능성이 증가한다. 우리의 물레방아가 회전을 멈춘다면, 다시 큰 크기의 유속이 오기 전까지 물레방아는 회전하지 않는다. 따라 서 회전을 멈추지 않는 것은, 지속 가능한 발전을 위해 매우 중요한 요소이다. 따라서 토크/회전 관성의 표준 편차가 작고 최솟값이 큰 4-Flap Version이 3-Flap Version보다 최적이다.

### 4. Modeling

4.1 물레방아 구조

4.1.1 물레방아 개략도

[Fig. 10] 물레방아 개략도, 부품 정의

[Fig. 11]: 물레방아 축 정의: AB-AT: Angle Block axial 두께 / FC-AT : flap cap 축 방향 두께 / G-AT : 기어 축방향두께 / LAG-AT: Linear Angle Guide Axial Thickness


[Fig. 12] ADW Radial Dimension. ADW FF에서 Pin-Slot 거 리를 기재하였다. (-45~45 변역 기준)

4.1.2 부품 별 설계


[Fig. 13] Center body

Center body는 로터의 주 회전자로, Flap을 고정하며 회전할 수 있게 한다. 그와 함께 B-ALA를 고정하며 B-CRA위에서 회전한다.

[Fig. 14] LAG (Linear Angle Guide). 26-A : LAG가 조립된 모습. Angle Block에 연결되어 이동하면서 동시에 B-FPS에 연결되어 Flap의 각도를 정한다. 26-B : LAG의 모습.

LAG는 Bearing 방식으로, 철도에서 기차가 이동하 듯 AB위를 베어링을 통해 미끄러지듯 이동하며 Flap의 각도를 제어하게 된다.


[Fig. 15] 28-A: Straight Flap, 28-B: StraightFlapWF, 28-C: Half Capsule Flap, 28-D: Full Capsule Flap

- 5 -

### 5. 물레방아 제작

5.1 전반적인 제작과정
위에 | 서술한 | 부품들은 | 전부 | 학교 | 3d | 프린터
(Ultimaker 3 Extended, Ultimaker 2)로 제작되었다. 수 차의 중심축에는 직경 6mm 카본 파이버 봉을 사용하 였고 Flap과 중심의 연결에는 2mm 카본 파이버 봉을 사용하였다. 카본 파이버 봉의 단단하면서도 가벼운 특 성은 수차의 경량화에 기여했으며 결과적으로는 수차의 효율을 증가시켰을 것으로 예상한다. 봉들은 다시 부품 들과 회전을 위해 베어링으로 연결되고, LAG의 경우 수직적인 움직임을 위해 리니어 부싱과 연결되어 자유 로운 수직 움직임을 가지도록 한다. 최종적으로 외부프 레임의 경우 수차의 무게를 버티며 Angle Block이 휘 지 않게 하기 위해 휘지 않으며 무게를 지탱할 수 있는 알루미늄 프로파일을 사용하였다.

위와 같은 재료들을 사용하여 이와 같은 순서로 제작 하였다.
1. Flap과 중앙 프레임의 연결
2. LAG의 연결
3. 중앙축(6mm 봉) 끼우기
4. 외부프레임과 Angle Block 연결
5. Angle Block에 중앙축 끼우기
6. 외부프레임 조립과 길이 조정
앞으로 총 4개의 새로운 모델을 소개하겠지만, 모든 모델은 5.1에 서술된 제작과정을 따랐다.

5.2 Models
5.2.1 Prototype


[Fig. 16] Prototype

첫째로 만든 Prototype이다. 세 개의 평평한 플랫을
사용하였다. | Application의 | 효율 | 개선에서 | 설명될
Magnet model의 방향을 적용하였지만, magnet 방식의 한계점과 저항에 비해 작은 힘으로 인해 회전하지 않았 다.

5.2.2 3-Flat Version


[Fig. 17] 3 FLAT MODEL

Test bed에 들어갈 수 있는 최대 크기로 플랩의 크기 를 대폭 증가시켜 받는 힘을 늘렸고 Center Frame에 사용되는 필라멘트의 감소, 필라멘트가 채워져 있던 기 존 방식에서 틀 위에 셀로판지를 붙이는 방법으로 경량 화 시켰다. 또한, 프로토타입과 다르게 3 FLAT MODEL에서는 Magnet 방식이 아닌 Bearing 방식을 택함. 센터바디 일렬이 안되는 문제를 해결하기 위해 외부 프레임을 알루미늄 프로파일로 바꾸기도 하였다. 이 모델의 경우 6.1.1 에서 설명될 자체제작 Test Bed 에서 회전을 확인하였다. 처음으로 이론의 검증이 이루 어진 모델이다.

5.2.3 4 FLAT MODEL


[Fig. 18] 4 FLAT MODEL

4개의 Flat Flap을 이용한 모델. 시뮬레이션 결과와 정성적 예측을 통해 flap의 개수를 늘리는 편이 효율을 확실히 증가시킬 것이라는 결론을 내렸다. 하지만 flap 의 개수를 더 늘렸을 때의 경우에 대해서는 flap 간의 간섭(물의 흐름에 의한), 경제성 측면에서 우려되어 5 개 이상은 시도하지 않았다.


- 6 -

5.2.4 4 CURVE MODEL


[Fig. 19] 4 CURVE MODEL

Curved Flap 4개를 사용한 모델. 반원모양의 flap을 사용하게 될 경우, 물로부터 더 큰 에너지를 얻을 것이 라는 아이디어에서 발전하여 제작하였다.

### 6. Experiment

6.1 실험 장소

실험은 총 두곳에서 진행되었다. 먼저, 접근성이 높은 대신 물의 흐름이 완전히 일정하지 않고 유속이 고정된 직접 제작된 Test bed, 둘째로는 완전히 균일한 유속을 제공하고 이에 더해 유속을 미세 조정할 수 있는 Endless Pool에서 실험을 진행하였다.

6.2.1 자체제작 Test Bed

첫째로 직접 제작한 Test Bed의 형상은 다음과 같다.


[Fig. 20] Test Bed의 모습

직접 제작한 Test Bed는 위와 같이 거대한 수조 세개에서 위치에너지로 인해 호스를 통해 물이 세개의 구멍으로 들어오고 이가 다시 반대편에 있는 여러 개의 작은 구멍을 통해 나오게 되면서 수조 안에서는 한방향으로의 물의 흐름이 발생하게 된다. 수조는 아크릴판을 레이저 커팅기로 자른 후 실리콘칠을 통해서 제작하였다.

6.2.2 Endless Pool

두번째로는 Endless Pool로 이번 연구에 활용된 모델은 Endless Pools사의 Dual propulsion pool이다. Endless Pool은 여러 작은 호스에서 물을 강하게 밀어내기 때문에 매우 균일한 유속이 발생하고, 때문에 실제 환경과 유사하다 생각할 수 있었다. 더 나아가, 엔드리스 풀은 유속을 변화시킬 수 있다는 점에서 큰 강점이 있었다. 하지만 이가 우리의 소유가 아니라는 점에서 시간의 제약과 공간의 제약이 있었다.

[Fig. 21] Endless Pool 사의 Dual propulsion model

6.3 실험 과정
6.3.1 유속에 따른 평균 각속도 측정
앞서 제작한 4 FLAT 모델과 4 CURVE 모델의 효율성을 비교하고, 실제 환경에 가깝다 볼 수 있는 충분히 낮은 유속에서도 제작한 물레방아가 잘 작동하는지를 살펴보기 위해 총 8개의 다른 유속 3, 5, 7, 15, 22, 30, 37, 45 (100이 1:08/100yard)에서 FLAT과 CURVE를 각각 실험해보고 이에 대해 영상을 촬영한 후 평균 각속도를 측정한다.
6.3.2 토크에 따른 평균 각속도
전의 실험으로 4 CURVE가 가장 효율적인 모델임을 확인 후, 이가 얼만큼의 부하를 걸었을 때 최대 전력을 생산하는지 알아내기 위해 이와 같은 실험을 고안하였다. 물론 가장 이상적으로는 각 부하마다 얼만큼의 전력을 생산하는지 정확히 알아내는 것이 이상적이지만 이는 현실적으로 어려움이 따르기에 그 대신 우리는 수차에 도르래를 달아 인위적으로 부하를 주고 각 무게마다 돌아가는 각속도를 측정하여 이를 이용해 전력을 예상했다. 아래 식에서 m은 수차에 가한 추의 무게, r은 도르래의 반지름.
| P(W) = mgrω
이러한 실험은 오랜 시간이 요구되는 특성상 자체 제작된 Test Bed에서 실행되었다.

[Fig. 22] 도르래 메커니즘


- 7 -

위와 같이 실에 무게추를 달면 이러한 부하는 Timing Belt를 통해 수차의 중심축에 직접적으로 연결되어 부하를 그대로 전해줄 수 있다. 이러한 추가 물 속에 들어가게 되면 부력의 영향을 받기에 추는 수조 밖으로 빼내서 실험했다. 추는 100g 부터 시작하여 100g 단위로 수차의 회전이 완전히 멈추는 것으로 보일때까지 계속 추의 무게를 추가하여 측정하였다.

### 7 Conclusion

7.2 유속과 평균 각속도 간의 관계

[Fig. 23] 유속에 따른 평균 각속도의 변화. 파란색은 4 Curve 모델, 붉은색은 4 Flat 모델을 나타낸다.

Endless pool에서 진행한 실험으로 몇 가지 유의미한 결과를 도출할 수 있었다.
첫째로, 자체제작 Test bed에서는 확인했던 결과이지만 Endless pool이 구현하는 거의 완전하게 균일한 물의 흐름에서 두 모델 모두 성공적으로 회전하였다.
둘째로, 4 FLAT 모델과 4 CURVE 모델로 8개의 유속에 대한 평균 각속도 비교를 진행한 결과, 유의미하게 curved가 나은 효율을 나타냄을 보일 수 있었다. 반원모양의 flap이 더 큰 힘을 전달할 것이라는 예측이 맞은 셈이다.
셋째로, 유속에 따른 각속도의 관계는 선형으로, 저유속에서도 회전 가능함을 알 수 있었다. 이는 우리의 수중 물레방아가 저유속인 강 (금강: 5.5cm/s, 낙동강: 15.5cm/s) 에서도 충분히 사용될 수 있음을 보여준다.

7.3 토크와 평균 각속도 간의 관계

[Fig. 24]: 가한 추의 질량과 그에 따른 평균 각속도의 감소를 나타낸 그래프.

먼저, 최대 1300g의 부하를 걸었을 때까지 회전을 관찰할 수

있었고 1400g 부터는 온전한 한 바퀴의 회전이 일어나지 않았다. 때문에 100-1300g 까지의 부하에 대한 평균 각속도를 측정하였는데, 그 결과는 위와 같다.

[Fig. 25]: 평균 각속도와 전력 사이의 그래프로 재구성. 세로 실선은 전력이 최대가 되는 때.

추의 무게(g)와 평균 각속도(rad/s) 사이 관계를 나타낸 그래프를 Power와 평균 각속도 사이의 그래프로 변환하게 되면, 전력과 평균 각속도에 대한 관계를 나타낸 그래프를 얻게 된다. 800g의 부하를 걸었을 때 최대 전력인 0.043W를 수중 물레방아가 생산할 것으로 계산되었다. 즉, 이 조건에서 가장 효율적으로 작동하는 부하는 800g인 것이다. 가장 효율적으로 작동하는 부하는 유속에 따라 변화할 것이기에 이는 어디까지나 Test bed의 유속 (0.19m/s 추정) 에서의 최적화이다. 우리는 특정 유속에서 최대 전력을 생산하는 부하를 찾는 메커니즘을 하나의 유속에서 제시하는 것으로 전력에 대한 분석을 마무리한다.
아래 사진은 두가지 실험에 대한 결과를 3차원 그래프에 plotting한 데이터이다.

[Fig. 26] 유속, 평균 각속도, 전력 사이의 3차원 그래프

- 8 -

### 8 Application

8.2 효율 개선
8.2.1 자기부상
Angle Block을 따라 LAG가 베어링을 통해 미끄러지면서 이동하는 방식을 우리는 기존의 Bearing model이라 불렀다. 이러한 방식은 제작에 용의하고 적은 비용을 요구하였지만 그와 동시에 베어링이 오랜 기간 사용시 녹슬 수도 있다는 점, LAG의 베어링과 Angle Block 사이에 마찰이 항상 존재한다는 점이 효율을 감소시키고 있었다.
때문에 여기서 새롭게 제시하는 Magnet model에서는 이러한 약점을 보완한다. Magnet model은 Bearing의 미끄러짐이 아닌 자기부상열차와 같이 LAG가 자석 간의 반발력으로 인해 Angle Block을 따라 미끄러지는 원리이다.


[Fig. 27] Magnet model을 택할 경우 LAG가 Angle Block에 따라 이동하는 모습

이를 적용할 경우, 수차의 가장 큰 자체 저항 발생 원인이었던 Angle Block과의 마찰을 해결한 것임으로 효율을 크게 증가시킬 것으로 기대된다.
하지만 Magnet model로 제작해본 수차들은 오히려 제대로 돌아가지 못하는 모습을 노출했는데 그 원인은 다음과 같다.


[Fig. 28] LAG의 자석과 Angle Block의 자석이 계속해서 붙는 모습

LAG 회전 중 Angle block의 자석과 LAG의 자석이 붙어버리는 문제가 발생한 것이다. 이는 제작 과정에서 연속적인 원형의 큰 자석을 사용한 것이 아닌 이산적으로 여러 개의 자석을 설치하였기에 생긴 문제로 보인다. 원래 의도대로라면, 모든 위치에서 Angle block의 자석은 LAG의 자석에 동일한 척력을 제공하며 자기부상열차와 같은 움직임을 보여야 했지만 이산적으로 배치된 배열은 일정한 척력이 아닌, 어떤 부분에서는 인력을 나타내게 되었고 이러한 문제가 발생하게 되면 회전이 불가능하게 된다. 때문에 본 연구에서는 그 이후 만든 모든 model을 bearing model로 만들게 되었다. 하지만 이를 강자성체로 감쌀 수 있다면 이러한 문제를 해결할 수 있을 것으로 보인다. 외부를 강자성체로 감싼 angle block은 외부에서 안정적인 자기장을 만들어낼 것이고, 때문에 angle
block과 | lag의 자석 사이에 | 일정한 척력은 | 기존의
아이디어였던 자기부상열차와 같은 최소한의 저항을 가능케 할 것으로 보인다.


[Fig. 29]: Angle Block의 강자성체 감싸기를 통한 자기장 안정

8.2.2 Angle Block 최적화
Angle Block의 최적화로도 효율 증가를 꾀할 수 있다. 다음과 같은 개선 방법 최적화를 거쳐야하는 것으로 보인다.
1. 유속에 대한 Flap 각도별 Torque 계산
2. Rotor 각도에 대한 회전축 최대
3. Smoothing (인접 노드 산술 평균 방식)
이는 다변수에 대해 CFD를 돌려야 하기 때문에 많은 계산양을 요구하기에 현실적으로 이번 연구에서는 배제하였다. 하지만 angle block 최적화는 불균형 토크를 최대화하며 더 나은 효율로의 발전을 가능케 할 것이다.

8.2.3 대형화
우리가 도출한 효율은 저항, 최적화 미진행의 원인도 있지만
크기의 | 문제로 | 더 | 많은 | 전력을 | 생산하지 | 못했다.
40cm*40cm*40cm의 크기에 맞춰 제작된 현재의 수중 물레방아는 소형발전기로 규정된 5m*5m*5m의 크기에 한참
덜 | 미친다. | 때문에 | 소형발전기의 | 범주에서 | 벗어나지
않으면서도 크기를 10배 이상 키울 수 있으며 풍력발전기 VAWT (vertical axis wind turbine)에서 진행되었던 선행연구에 따르면 날개의 면적에 비례하여 전력이 생산됨을

- 9 -

우리의 수중 물레방아에 동일하게 적용, 총 100배 이상의 전력량 개선을 할 수 있을 것으로 보인다. 이러한 유추는 VAWT와 수중 물레방아가 토크를 얻는 방식이 유사하다는 점에서 착안 면적에 비례한다는 사실은 충분히 신뢰 가능한 것으로 보인다.

8.3 기존 방식과의 비교
수중흐름을 사용하여 에너지를 생산하는 방식으로 현재 사용되고 있는 기술은 Underwater windmill, 다른 말로 tidal stream turbine이라 불린다. 우리가 고안한 캠 구조, 수동적 날개 조정 시스템과 이는 차이가 있기에 여기서부터 혼동을 피하기 위해 기존의 방식을 tidal stream turbine이라 부르겠다. Tidal stream turbine은 가장 잘 알려진 형태의 풍력발전기와 동일한 원리를 가지고 물속에서 가동하도록 변형시킨 것이다.


[Fig. 30]: 사용되고 있는 Underwater Windmill
이러한 기존 방식과 비교하여 우리의 수중 물레방아는 강점을 보이는데 이를 서술하겠다.

8.3.1 수중, 수상 환경 분석
가장 주목할만한 점은 수중 물레방아의 긍정적인 환경적 영향이다. 기존 Tidal stream turbine의 약점이 설치된 위치 500m 반경에 있는 수중환경에 악영향을 끼쳤던 것과 달리, 새롭게 개발된 수중 물레방아는 오히려 환경적으로 이득일 것이다. 이는 수중 물레방아가 위아래로 물을 섞어주는 역할을 하기 때문인데, 수중 물레방아의 형태에서 알 수 있듯, 축이 지면과 수평하게 놓여짐으로 인해 수중 물레방아는 물의 수직적 움직임을 발생시킨다. 이는 영양염류의 순환으로 이어지며 녹조 제거로까지 이어지게 된다. 현재 강의 녹조제거를 위해 물순환 장치를 이용하고 있는데, 새롭게 고안된 물레방아는 물순환을 진행시키면서 동시에 에너지를 생산할 수 있는 것이다.
또한, 수중환경에 가해지는 위협에 대해서는 적게 우려된다. 먼저 수중 물레방아는 물 속에서 발전을 위해 부하까지 걸어주게 되면 느린 속도로 회전한다. 그리고 물고기들의 이동방향을 가로막는 것이 아닌 그와 같은 방향으로 회전하고 있기에 아직 검증은 필요하지만 수중 생태환경에 악영향을 최소화할 수 있을 것으로 보인다. 수상환경에 대해서는 배가 위로 자유롭게 지나다닐 수 있기 때문에 경제적 이점 또한 기대된다. 이러한 장점들을 아래의 그림으로 도식화하였다.

[Fig. 31] 환경적 이점의 도식화

또한, 기존 방식이 조석을 이용한 빠른 유속에서 적용되었다면 우리는 앞선 실험을 통해 매우 느린 유속에서도 수중 물레방아가 발전 가능함을 보였다. 때문에 이는 느린 강에서도 친환경에너지를 생산하는 혁신으로 보인다.
9. 결론

본 연구에서는 수동적 날개 조정 시스템을 위한 캠 구조 수중 물레방아를 제작하였다. 제작한 물레방아는 환경적인 면에서, 그리고 에너지 생산적인 면에서 모두 우수하였다. 제작한 4-Curved Version은 43mW의 발전이 가능하였으며, 40cm 스케일에서 10m 스케일로 증가했을 때 26.875W의 전력 생산이 가능할 것으로 추정된다. 또한 본 연구의 물레방아는 수중에서는 해양 생태계에 큰 간섭을 하지 않고, 수상에서는 배의 이동에 간섭을 하지 않는 큰 환경적 이점이 있다. 또한 물을 섞어 녹조를 제거하고 영양염류를 희석시키는 이점도 존재한다.
향후 연구로는 마찰 감소 방법 연구, 캠 구조 최적화, 대형화가 있으며, 이러한 연구들을 통해 발전량을 증가시킬 수 있을 것으로 기대된다.

### References

[1] Eriksson, S.; Bernhoff, H.; Leijon, M. (2008). "Evaluation

of different turbine concepts for wind power". Renewable

and Sustainable Energy Reviews. 12 (5): 1419–1434.
[2] Ministry of Land, Infrastructure and Transport Han River Flood Control Office, Report on Flow Measurement of Han River (Lower Section) and Imjin River Watershed (2000)
[3] Uihlein, A., & Magagna, D. (2016). Wave and tidal current energy–A review of the current state of research beyond technology. Renewable and Sustainable Energy Reviews, 58, 1070-1081.

- 10 -

김 선 재(Sunjae Kim)

- 2022년 2월 : 서울 대명중학

교 졸업

- 2022년 3월~현재 : 한국과학

기술원 부설 한국과학영재

학교 재학

<관심분야>
에너지 하베스팅, 시뮬레이션

유 지 함(Jihahm Yoo)

- 2022년 2월 : 서울 역삼중학

교 졸업

- 2022년 3월~현재 : 한국과학

기술원 부설 한국과학영재

학교 재학

<관심분야>
에너지 하베스팅, 응용수학, 수학적 모델링

조 용 우(Yongwoo Cho)

- 2022년 2월 : 서울 서일중학

교 졸업

- 2022년 3월~현재 : 서울과학
고등학교 재학

<관심분야>
기계공학, 로봇공학, 컴퓨터공학

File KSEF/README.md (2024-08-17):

# KSEF 저유속 수차 연구 프로젝트 

이 저장소는 KSEF(Korea Science & Engineering Fair)에 출품한 저유속 수차 연구 프로젝트의 자료를 포함하고 있습니다. 이 프로젝트는 한화 사이언스 챌린지에서 진행한 연구를 발전시킨 것입니다.

**KSEF 실험 영상**


## 목차

1. [빌드 파일 (BUILD)](#빌드-파일)
2. [코드 분석 (Code Analysis)](#코드-분석)
3. [치수 설계 (DIMENSION)](#치수-설계)
4. [문서 (Documentation)](#문서)

## [BUILD : 설계 파일](./BUILD/) 🏗️🔧

이 섹션에는 프로젝트의 빌드 관련 파일들이 포함되어 있습니다:
- 경량 노출 자석 버전 : 자석으로 효율화를 시도하였으나 실패한 버전의 모델링
- 최종 작동 버전의 모델링이 포함되어 있습니다.
- 1차 소형 버전 : 크기가 작아 실패한, 초기 프로토타입의 모델링입니다.

## [Code Analysis : 코드 분석](./Code%20Analysis/) 💻📊

수차 설계를 위한 코드가 여기에 있습니다.
- DIMENSION : 치수 설계를 위한 코드
- Magnet Version/자석 버전
  
  목적 : 작은 직사각형을 자석을 여러 개 배치하여 Angleblock의 형상을 만들자!

  DXF 파일의 역할 : 자석을 꽂을 수 있는 DXF를 만드는 코드.

  - DXF_V1 : LAG 경량화 이전, 초기 코드
  - DXF_V2 : LAG 경량화 이후, 버전 2
  - DXF_V3 : LAG 경량화 이후, 버전 3

## 문서 📚📑

프로젝트 관련 문서 파일들:
- KSEF 2023 저유속 수차 연구 논문.pdf: 연구 결과를 정리한 논문 파일 📄
- KSEF 발표자료.pptx: KSEF 대회 발표에 사용한 프레젠테이션 파일 🎭

이 문서들은 저유속 수차 연구의 발전된 내용, 새로운 연구 결과, 그리고 KSEF 대회를 위해 준비한 발표 자료를 포함하고 있습니다.

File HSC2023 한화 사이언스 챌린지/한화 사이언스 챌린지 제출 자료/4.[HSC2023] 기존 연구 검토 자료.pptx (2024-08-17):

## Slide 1

작성 방법 안내

본 자료는 토론 발표 심사 시 활용되는 자료로서,
기존 연구 결과와 유사한지, 유사하다면 어떻게 발전시켰으며
다르다면 어떤 점이 다른지와 연구 착안에 대한 팀의 생각을
충분히 파악하기 위한 중요한 자료입니다.
페이지수는 2장으로 제한됩니다.
작성된 자료는 8월 11일 (금) 자정까지 운영사무국 이메일로 보내주시기 바랍니다.
*제출 시간을 넘길 경우, 심사에 불이익이 있을 수 있으니 제출 시간을 지켜주시기 바랍니다.
※이메일 주소 첨부

1) 구분: 예선 접수 시 선택한 적용 과학 기술 분야 기입
2) 기존 연구 내용 요약: 간략하게 3~4줄로 해당 연구의 내용을 요약 기술
3) 기존 연구와 우리팀 연구의 차별성: 토론 발표 심사 시, 각 팀의 연구 내용 발표 전 해당 내용을 바탕으로
심사가 진행됩니다. 기존 연구를 바탕으로 우리팀이 본 연구를 시도하게 된 계기, 착안점, 기존연구와의
차별성 등을 정확하게 기술해주시기 바랍니다.
4) 기존 연구 링크: 1페이지에서 언급한 연구 링크 및 팀 별 연구 시 참고한 연구 링크 (최소 3개, 최대 5개)

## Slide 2

기존 연구 검토 자료

No. | 구분¹⁾ | 팀명 | 연구주제 | 비고
1 | 1 | 피쉬파워 | 저유속에서 발전 가능한 접이식 날개 수차

구분 | 내용
기존 연구 (연구명, 연구자, 연구년도) | 특허 10-1197360 , 수정 날개 접이식 수차, 홍문표 , 2010년
기존 연구 내용 요약²⁾ | 기존의 접이식 날개로 사용한 수차의 요약이다. 1.수정 날개 접이식 수차는 날개를 접어서 발전을 하는 방식이다. 2.날개는 자유로이 회전하나 가동범위가 제한되어있고 유도판과 롤러로 접힘이 제어된다. 3.유도판의 제어를 통해 복류식 발전이 가능하다. 4.댐에서 작동하도록 설계되어 있으며 저낙차 발전효율 상승을 고려한 구조이다.


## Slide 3

기존 연구 검토 자료

No. | 구분¹⁾ | 팀명 | 연구주제 | 비고
1 | 2 | 피쉬파워 | 저유속에서 발전 가능한 접이식 날개 수차

구분 | 내용
기존 연구 내용 요약²⁾ | 단점 1. 유도판(102)와 날개의 마찰, 충격으로 인해 날개의 변형과 파손이 초래될 수 있으며 발전효율에 손실이 있다. 2. 하나의 날개가 유도판에 의해 펴지지 못해 그 이후 날개들이 연쇄적으로 접히게 되어 유도판에 가해지는 부하가 커져 내구도가 약해지게 된다. 3. 수차 집에서 벗어난 날개가 다시 펴져 회전력을 발생하기 위해서는 임계각에 도달해야 하기 때문에 회전력을 발생시킬 수 있는 영역이 줄어들게 된다.


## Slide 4

기존 연구 검토 자료

No. | 구분¹⁾ | 팀명 | 연구주제 | 비고
1 | 3 | 피쉬파워 | 저유속에서 발전 가능한 접이식 날개 수차

구분 | 내용
기존 연구와 우리팀 연구의 차별성³⁾ | 우리의 연구 목적은, 강에 댐 없이 사용 가능한 저가형 수력 발전기를 만드는 것이다. 따라서 해당 연구의 장점 중 복류식으로 발전 가능하다는 장점은 우리의 적용처에는 필요가 없다. 강의 흐름은 대부분 일정하기 때문이다. 또한, 2에서 언급된 장점들 모두 강이라는 특수한 적용처에 의해, 매우 넓고 유량이 크다는 특성에 의해 비교 무의미 해진다. 우리의 구조에는 입수구와 출수구를 제한하는 시멘트 구조물 (특허의 수차집 (24))이 없다. 대유량 설비에서 이러한 시멘트 구조물을 사용하는 것은 친환경적이지 못할 뿐만 아니라 비용과 공사시간을 늘린다. FRW에서는 특허에서의 고정턱이 아닌, 물의 흐름에 완전히 맡겨 날개가 자연스레 접히게 하였고, 따라서 날개에 치명적인 영향을 줄 수 있는 충격과, 발전효율에 악영향을 미치는 요소를 줄였다. 하지만 FRW에서는 발전효율을 감소시키는 역방향 토크를 최소화 시키지는 못한다. 물의 유속이 FRW의 Flap을 접는데 사용되기 때문이다. 이러한 역방향 토크를 최소화하고 최적화하기 위해 ADW를 만들었다. ADW는 Flap의 특성에 맞추어 Angle Block의 형상을 조정해 역방향 토크를 최소화하고 출력을 최대화 시킬 수 있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

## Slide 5

기존 연구 검토 자료

No. | 구분¹⁾ | 팀명 | 연구주제 | 비고
1 | 4 | 피쉬파워 | 저유속에서 발전 가능한 접이식 날개 수차

구분 | 내용
기존 연구 링크⁴⁾ | URL 1 | https://patentimages.storage.googleapis.com/pdfs/49f74b20db13ad10ce25/1020100027024.pdf
| | 설명 : 특허 pdf
| URL 2
| | 설명 :
| URL 3
| | 설명 :
| URL 4
| | 설명 :
| URL 5
| | 설명 :

타 대회 중복 수상 여부 | 없음

※ 기타 사항

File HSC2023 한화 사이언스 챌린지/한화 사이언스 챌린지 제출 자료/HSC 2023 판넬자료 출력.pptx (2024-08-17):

## 물레방아를 접자!

1. 기본적인 물레방아
발전 영역이 전체 수로를 활용하지 못함, 낮은 효율
2. 물레방아를 다 담구면?
발전 영역은 커지지만, 대칭적인 저항으로 인해 회전 X
3. 접어서 해결하자!
발전 영역에 손실도 없으며, 여전히 회전하게 된다.


## 기존 연구 – 수정 접이식 수차 특허의 단점


1. 유도판과 날개의 마찰, 충격
날개의 변형과 파손이 초래됨.
2. 하나의 날개가 접힐 때 그 이후 날개들이 연쇄적으로 접히게 되어, 유도판에 가해지는 부하가 커져 내구도 약화.
3. 수차 집에서 벗어난 날개가 다시 펴져 회전력을 발생하기 위해서는 임계각에 도달해야 함. 해당 특허에서는 임계각을 고려하지 않음.


## 피쉬파워의 연구는 무엇이 다른가?

1. 입수구와 출수구를 만드는 시멘트 구조물 없음!
-> 친환경적, 저비용과 빠른 공사기간.
2. FRW, 물의 흐름에 완전히 맡겨 날개가 자연스레 접힘.
-> 날개의 내구도 개선, 충격 없앰.
3. ADW 구조로, Angle Block을 통해 최적 성능 각도 구현
-> 기계적으로 구속되는 구조, 최대의 성능 얻어냄.

Building without Concrete? - Commentaries

## 수력 발전의 뉴 패러다임, ADW

물레방아 < 사진/그림 뉴스 < 문화/예술 < 기사본문 - 시니어 타임스(Senior Times)

댐 :
1. 엄청난 양의 콘크리트
2. 큰 건설 비용
3. 수생태계의 파괴
물레방아 :
1. 물 위로 튀어 나옴.
2. 폭을 확장하기 어려움.
3. 낮은 발전 효율

댐 없이 발전 가능
콘크리트 없이, 적은 건설 비용.
수생태계 파괴 없음
물 안에 완전히 담겨서 구동.
광폭 수로에서 발전 용이
물레방아에 비해 동 면적 2배의 효율을 가짐.

댐 넘친 건 역대 두번째… 1980년에도 괴산댐이었다

## CFD & 코드 최적화


어떠한 날개가 최적의 결과를 내줄까요?
어떠한 각도 분배가 최적의 결과를 내줄까요?

30cm 정육면체, 1m/s Water Flow Test
날개 각도에 따른 힘 데이터 수집
모든 날개의 각도를 제어할 수 있는 수차, ADW
CFD 힘 데이터와 모멘트암을 계산하여 최대 토크각도 배분을 구함.
Smoothing을 통해 실사용시 안정성 타협함.
: K번째 요소는 K+1와 K-1 요소의 평균으로 업데이트!


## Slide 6

결과
CFD 데이터를 바탕으로, 토크는 FullCapsuleFlap의 최적화 ADW에서 최대 40%, 평균적으로 12%의 향상이 있었습니다. 물 내부는 저항력이 높은 환경이므로, 회전수가 토크에 비례합니다. 따라서, 저희의 수차는 최대 2배, 평균적으로 1.4배의 발전량 개선을 거뒀습니다.
실험을 통해 ADW의 구조가 실현 가능함을 확인하였으며, 더 높은 정밀 제작을 통해 실제 이론에 근접한 효율을 얻어낼 수 있을 것입니다!

동면적 200%의 발전량
광폭 수로 적용 가능!
수상 선박 정상 운행 가능!

NO 큰 초기비용!
NO 수생태계 파괴!
NO 저효율 물레방아!

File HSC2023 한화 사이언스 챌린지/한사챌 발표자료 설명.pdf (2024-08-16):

# 연구발표자료 - 1


저희의 연구 목표는 느린 유속에서 값싸게 발전가능한 지속 가능한 에너지를 만들어내는 것이었습니다.

이러한 목표를 달성하기 위한 아이디어로 물레방아를 떠올렸습니다. 그런데, 물레방아는 강물에 담겨 발전하게 되는 단면적이 적어 강물의 에너지를 한껏 쓰지 못하는 한계가 있습니다. 저희는 강물의 에너지를 최대한 사용하길 원했고, 우선 물레방아 전체를 물에 담그는 방법을 고민했습니다. 그런데, 물레방아를 그대로 물에 담그면 상하 대칭적인 구조로 토크가 상쇄되어 회전하지 않습니다.

그러나, 물레방아의 위쪽 있는 날개를 접으면 단방향 토크만 생기게 되어 수차가 회전하게 될 것이란 아이디어가 생각났고, 이를 발전시켜 두 가지 접이식 수차를 개발하게 되었습니다.


접이식 수차를 본격적으로 개발하기 이전에 접이식 수차에 대한 기존 연구를 검색해 보았습니다. 기존 연구와 중복되는 연구인지 혹은 기존 연구를 참고하여 개선할 만한 점이 있는지를 확인하기 위한 과정이었습니다.

찾아보니 댐에 적용될 수 있는 접이식 수차에 대한 특허가 있었습니다. 이 특허를 자세히 검토해보니 특허 출원자가 충분히 고려하지 못한 다양한 문제를 발견하게 되었습니다. 기존 접이식 수차의 원리는 위쪽 날개는 전부 펴지고, 아래 날개는 전부 접혀 회전력을 만들어내는 원리로 날개와 유도판의 "충돌"을 이용해서 날개를 접습니다. 그런데, 강한 충돌로 인해 날개와 유도판의 내구성에 문제가 생기며, 유도판의 굽은 형상으로 인해 회전력 발생 영역이 크게 감소하여, 실제로는 특허 본문에 언급된 것과 다르게 작동합니다.

저희는 이러한 점을 보완하여 각도 접이식 수차를 개발하였습니다. 즉, 날개의 위치에 따라 각 날개의 각도를 다르게 조정하였으며, 충돌 없이 지속가능한 형태의 높은 내구성을 가진 접이식 수차를 개발하였습니다.


저희가 개발한 수차는 | 댐이나 기존 연구와는 달리 | 시멘트 구조물을 사용하지 않고
오로지 수차만으로 발전할 수 | 있기 때문에, | 친환경적이고, 비용도 적게 들며,
빠르게 공사할 | 수 있어, | 개발도상국에 적용하기 매우 적합합니다.

또한, 접이식 수차에 대한 기존 연구에서 사용된 방식인 유도판을 통해 기계적 마찰을 일으켜 날개를 접는 방식 대신 제한된 범위 내에서 자유롭게 움직일 수 있는 날개 구조로 물의 흐름에 의해 자연스레 날개가 접히고 펴지는 FRW (Free Rotating Wheel) 구조를 제안해 유도판과의 충돌 과정에서 발생하는 내구도 문제를 해결했습니다.

Angle Defined Wheel(ADW)로는 자동차의 Cam 구조와 유사한 Angleblock을 통해 어느 위치에서든 최적의 성능을 발휘할 수 있도록 했습니다. 이로써 일반적인 물레방아에 비하여 동면적 2배의 발전 효율을 거둘 수 있습니다.


저희가 개발한 수차는 두 가지 수력발전 방식과 대조하여 개선점을 가집니다.

첫째로, 댐입니다. 댐은 수생태계를 파괴하여 친환경적이지 않고, 초기 투자 비용이 큰 수력발전임에 비하여, 저희가 개발한 수차는 댐을 짓지 않아도 되기에 더 개선된 경제성을 가지고 있고, 물고기들의 생활 환경에 피해를 거의 끼치지 않습니다.

둘째로, 물레방아입니다. 물레방아는 물 위로 튀어나와 있어 수상운송수단의 이동이 제한되며, 미관 상 좋지 않습니다. 또한, 깊은 물에 도달하기 어려워 수로의 깊이 또한 완전히 활용하지 못합니다.

저희 수차는 "접이식 수차의 뉴 패러다임"을 제시함으로써 이러한 문제를 완전히 해결했습니다. 물레방아의 장점인 저비용과 환경 친화적인 특성을 그대로 유지하면서, 수로의 폭과 깊이를 완전히 활용 할 수 있도록 개선하였습니다. 최적화시 동일 크기 물레방아에 비해 약 200%의 발전량을 얻을 수 있습니다.

# 연구자료발표 – 5


최적의 효율을 내기 위한 날개 형태 및 날개가 접히는 각도를 찾아내기 위해 Computational Fluid Mechanics로 시뮬레이션을 돌렸습니다.

한 모서리의 길이가 30cm인 물로 구성된 정육면체의 중심에 날개의 중심을 두고, 한 쪽 면의 유속을 1m/s, 다른 면의 압력을 0으로 두어, 유속 1m/s에서 날개의 각도에 따른, 날개가 물에 의해 받게 되는 힘을 구하였습니다.

이렇게 구한 Computational Fluid Dynamics(CFD) 각도 별 힘 데이터를 바탕으로, Angle Defined Wheel(ADW)의 각도 배분을 최적화 했습니다. ADW는 모든 날개의 각도 접힘을 제어할 수 있는 구조이므로, 코드를 통해 주어진 힘 데이터와 ADW의 구조에서 나올 수 있는 모멘트암을 계산하여 최적화된 각도 배분을 구하였습니다.

Smoothing 이란 이러한 최적화된 구조가 실제 사용시 부드럽게 구동될 수 있도록 평균 값으로 부드럽게 만들어주는 계산 과정입니다.

# 연구발표자료 – 6


저희 수차는, 일반적인 댐의 단점을 개선하고 수력 발전의 기본인 물레방아보다 효 율을 높인 미래형 수력발전입니다.

이를 위해, 일반적인 물레방아가 물에 정확히 절반만 담겼을 경우, 모든 영역에서 받을 수 있는 최대 토크의 합과 저희의 수차의 날개 별 최대 토크 합을 계산해서 비교해 보았습니다. 단순 토크만으로 비교하였을 때, 최대 40%, 평균적으로 12%의 향상이 있었습니다. 물 내부는 저항력이 높은 환경이므로, 회전수가 토크에 비례한 다고 가정해도 무리가 없습니다. 따라서, 저희의 수차는 동일한 날개 구조를 적용 한 물레방아에 비하여 최대 2배의 발전량 개선을 거둘 수 있었습니다.

일반적인 물레방아는 수면 위로 드러나 있는 부분이 매우 커, 설계상 폭을 매우 넓 게 하지 못하며 수상운송수단에도 제한을 줍니다. 하지만 저희 수차는 물에 완전히 담겨 구동되어 폭을 더 넓힐 수 있으며 물레방아보다 더 많은 물의 단면적을 활용 할 수 있는 구조입니다. 그와 동시에 댐의 초기 비용 또한 존재하지 않으며, 댐의 수생태계 파괴 또한 없앴습니다.

그렇기에 저희의 수차는 수력발전의 미래가 될 수 있습니다.

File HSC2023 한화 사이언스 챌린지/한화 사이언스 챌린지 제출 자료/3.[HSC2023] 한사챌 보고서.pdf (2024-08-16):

# 연구 진행 보고서

주제 | 저유속에서 발전 가능한 접이식 날개 수차

### 1. 서론

### A. 연구 배경과 목적

A.1 연구 배경

기존의 수력 발전 시스템은 빠른 유속의 강류나 높은 수위의 물의 에너지를 필요로 한 경우가 많았다. 하지만 이러한 조건을 갖지 않는 지역에서는 댐을 지어 인공적으 로 이러한 조건을 만들어야 했다. 또한, 기존의 빠른 유속을 사용하는 수력발전 방식 에서 발생하는 경제적 비효율, 환경적인 문제와 생태학적인 영향을 최소화하기 위해 서도 저속 유속 지역에서 수력 발전의 가능성을 탐구하는 것이 중요해지고 있다. 따 라서 본 연구는 느린 유속 지역에서도 효과적인 수력 발전을 실현하기 위해 접이식 날개와 cam 구조를 활용하여 새로운 발전 형태를 고안하고자 한다. 이러한 새로운 기술은 저속 유속에서 발생하는 환경적 문제를 최소화하면서 지속 가능한 에너지를 생성할 수 있을 것으로 기대된다.

A.2 연구 목적

본 연구는 느린 유속에서도 효과적으로 수력 발전을 가능하게 하는 혁신적인 방법을 개발하고자 한다. 접이식 날개와 cam 구조를 활용하여 터빈 전체를 물에 담 구어 발 전을 하는 발전 형태를 연구하고 있다. 이 연구의 주요 목적은 다음과 같다.

### 1. 느린 유속에서 발전할 가능한 환경 친화적인 수력 발전 기술 개발: 느린 유속 지

| 역에서도 효과적으로 수력 발전을 가능하게 하는 기술을 개발한다. 기존의 수력 발전의 제약을 극복하고 생태학적 보전과 함께 환경 문제를 최소화한다.

### 2. 지속 가능한 에너지 변환 메커니즘 최적화: FRW 와 ADW 구조 두가지 방식을

| 구현하여 물의 운동 에너지를 효율적으로 변환하는 메커니즘을 연구하고 최적화 한다. 이를 통해 발전 효율을 높이고 지속 가능한 에너지를 생산한다.

### 3. 경제적인 구축 가능성 평가: 느린 유속 지역에서의 수력 발전으로 지역사회 경제

| 와 생태계 보전에 기여하며, 지속 가능한 발전을 추구한다.

### 4. 다양한 지역사회에 긍정적인 영향 제고 : 느린 유속 지역에서의 수력 발전 기술

| 을 도입하여 에너지가 부족한 다양한 지역 사회에 긍정적인 영향을 제고한다.

### B. 선행연구 및 배경 자료

B.1 선행연구

B.1.1. 기존의 접이식 날개를 이용한 수력 발전 모델

대한민국 특허청에 등록된 특허 10-2010-0027024


Figure 1 : 수정 날개 접이식 수차의 간략한 구조 기존의 접이식 날개를 이용한 수력 발전 모델은 유도판을 사용하여 날개를 접어 토크의 차이를 발생시켜 발전을 하는 방식이다. 이 모델의 날개들이 유도판에 충돌을 하면서 날 개가 접히는 방식으로 설계를 하였다. 양쪽에 유도판을 설치하여 복류식으로 발전이 가 능하도록 설계하였고, 저 유속에서 높은 효율을 발전할 수 있도록 설계를 한 모델이다.

B.2 배경 자료

B.2.1 Pelton Turbin (펠톤 터빈)

펠톤 터빈은 물을 노즐로부터 분출시켜 위
치 에너지를 운동에너지로 바꾸는 수차로
충돌형 수차이다. 수압에 의해 버킷에 부
딪히는 물의 힘으로 회전력을 발생시킨다.
유량을 조정할 수 있는 기구를 갖추고 있
고, 유량조정이 최우선 되는 경우에 사용
할 수 있다. 펠톤 수차는 단류식 수차이다.

B.2.2 Cam Shaft (캠 샤프트 구조)

캠 샤프트는 내부 연소 엔진의 작동을 제어하는
중요한 부품 중 하나로, 밸브의 개방과 폐쇄를
조절하여 연소 과정을 조절한다. 카메라 샤프트
는 엔진 블록 내부에 위치하며, 엔진의 크랭크
샤프트와 동기화하여 작동합니다.

캠 샤프트는 여러 개의 커브 또는 로브로 구성되 어 있으며, 이 커브들은 밸브의 개방과 폐쇄 시 기를 결정한다. 엔진 작동 시, 크랭크 샤프트의


회전과 함께 카메라 샤프트도 회전하게 되며, 각 로브의 모양과 크기에 따라 밸브가 열 리고 닫히는 타이밍이 결정된다.

캠 샤프트는 크게 흡기 밸브와 배기 밸브의 작동을 제어하는 두 가지 유형으로 나뉜다. 인테이크 샤프트는 연료와 공기가 실린더 내부로 흡입되는 과정을 제어하며, 익스테이크 샤프트는 연소 후 배기 가스가 실린더에서 배출되는 과정을 제어한다.

### 2. 연구 방법

### 1. CFD 분석을 사용하여 날개 구조 별 유체의 흐름 분석

1. CFD로 날개가 받는 힘을 각도별로 측정한다.

### 2. CFD 데이터를 통한 분석

### 1. 날개의 각도 별 힘을 통해 위에서 구한 이론식에 대입하여 각속도를 계산할

수 있다.

2. ADW에서 얻어낼 수 있는 효율을 계산한다.

### 3. 흐르는 물에서 터빈의 토크와 회전 수 측정

1. 수조에 모터를 장착하여 한 방향으로 회전하는 물의 흐름을 만들어낸 다음, 터빈의 회전수를 측정한다.

### 2. 터빈과 연결된 프로펠러가 레이저를 차단하여 레이저 신호의 간격을 통해

터빈의 회전수를 구할 수 있다.

### 3. 연구과정

### A.본 연구의 설계

### A : 실험 장치 설계

A-1 : 전체 개략도


Figure 1 : 실험 장치의 전체 구성. 5-A : 실험 장치의 전체 구성, 어항 없음. 5-B : 실험 장치 구성 후면 5-C : 실험 장치 실제 모습

실험 장치의 목적은 강과 같은 환경을 제어 가능하게 해 실험 장치를 실험 가능하도록 하는 것이 다. 물의 직선 흐름을 만들기 위해 물이 내부에서 회전 가능하도록 사이에 칸막이를 설치하였다. 물은 모터를 이용하여 추진되며 유속을 조절할 수 있다. 실험 장치 윗면에 장착된 측정 장치들과 아두이노를 통해 토크, 회전수를 측정할 수 있다.

A-2 : 부분 별 설명

가. 모터 유체 추진

Figure 2 : 모터 유체 추진. 6-A : 알루미늄 프로파일에 모터가 결합된 모습. 6-B : 모터가 모터 마 운트를 통해 결합되어 있다. 6-C : 어항의 위에서 바라본 어항 속 유체의 흐름

나. 수차 결합 부

수차는 알루미늄 프로파일에 폭 310mm의 알루미늄 6mm 환봉을 통해 결합된다. 좌측은 20mm, 우측은 10mm의 고정부를 가지며, 베어링을 통해서 회전 가능하게 결합된다. Angle Defined Wheel(ADW)와 Free Rotating Wheel(FRW) 각각을 위한 별도의 수차 결합부가 존재한다.


Figure 3 : 수차 결합 부. 7-A: ADW) Angle Block Mount. 7-B: Barmount1, 7-C : Barmount3.

다. 가변 높이 축

회전수를 측정하기 위해 수차의 주 회전축 (B-CRA, Bar-Center Rotational Axis)를 수면 위로 꺼내 주고, 일정한 장력 을 제공하기 위해 가변 높이 축이 필요하다. 아크릴 판을 가 공해서 만들었으며, 나사를 돌려서 높이를 조절하고 고정할 수 있게 만들었다. 베어링 두 개로 축을 고정한다.


Figure 4 : 가변 높이 축

축의 한쪽은 수차에, 한쪽은 무게추에 연결되어 있어 모멘트암과 무게추의 무게를 이용해서 토크 를 구하게 된다. 그리고 회전수를 측정함으로써 걸리는 부하 (토크)에 따른 회전수와 이들의 곱을 통해 얻게 되는 에너지를 계산 할 것이다.

라. 수차 회전 수 측정기 (Wheel Tachometer)

수차 회전 수 측정기는 가변 높이 축에 검은색 아 크릴 날개를 단 이후, 레이저 모듈과 CDS 빛 감 지 센서 모듈을 이용해 회전수를 측정한다. 다음 과 같이 생긴 날개가 1회전시 2번의 레이저 깜빡 임을 CDS 빛 감지 센서 모듈에서 감지하고, 아두 이노는 이를 1초마다 세어 회전수를 계산하게 된 다.


Figure 5 : Wheel Tachometer의 모습. 아크릴 부품에 CDS 하고 레이저 모듈이 부착되어 작동한 다.

마. 유속 측정기 (Water Tachometer)

유속 측정기도 마찬가지로 같은 원리를 이용해 구동된다. 레이저 센서와 CDS 빛 감지 센서 모듈을 이용해 회전수를 측정하게 된다. 단, 물에 물레방아와 같은 회전자를 담 구어 물의 속도에 맞추어 회전하게 한다. 이때 수면의 높이에 따라 유속 측정기의 높이를 조 절할 수 있게 가변 높이 설계가 적용되어 있다.

Figure 6 : Water Tachometer.

바. 무게 추 가방

무게 추 가방은 토크를 측정하기 위한 장치이다. 들어간 추의 무게를 바꾸여가면서 토크를 바꾸 며, 이때 추의 무게와 회전수의 관계를 이용하여 추력을 비교한다.

Figure 5-C에서 무게 추 가방의 모습을 확인할 수 있다.

사. 아두이노 코드

아두이노 코드는 위의 기능을 효율적으로 수행하기 위해서 짜여 있다.

인터럽트 두 개로 Water Tachometer 하고 Wheel Tachometer의 기능을 수행하며, 노트북 과 시리얼 통신으로 데이터를 저장한다. 또한, 유속을 원하는 만큼 상승시키기 위해, 유속 이 같아질 때까지 모터에 가는 PWM 출력을 바꾸어 유속을 제어한다.

B : FRW 설명 (Free Rotating Wheel)

B-1 : FRW 개략도


Figure 7 : FRW 개략도, 축 정의

B-2 : FRW 정의


Figure 8 : FRW Axial Dimension, 축 방향 길이 정보.

gearAT : 기어의 축 방향 두께

FlapcapAT :Flapcap의 축 방향 두께

FlapAT : Flap (날개)의 축 방향 두께

S1 flapcap 과 flap 사이의 여분 공간

CenterPieceAT :CenterPiece의 축 방향 두께


Figure 9 : FRW Radial Dimension

B-3 : FRW 부품 별 설명

가. FF (Flap Frame)


Figure 15: 15-A: 45-90 FF. 45도에서 90도 회전 가능한 FF 15-B: 0-90 FF, 15-C: 0-45 FF.

S2 : gear와 barmount 사이의 두께

S3: space between FlapcapR & barmount

Black: Rotating Parts, drilled on to B-CRA

Blue: not rotating Parts, connected to B-CRA via Bearing

S: spaces (needs to be bigger than 1mm)


Figure 16 : 15-D: 0-45 FF에서 0도. 15-E : 0-45 FF에서 45도. 15-F : 0-90 FF에서 90도.

나. FC (Flap Cap)

Figure 17 : FRW FC (날개 수 3, 4, 5) (Left & Right) 이다.

Flap Cap은 B-FRA를 CB에 고정하는 역할을 한다. Left FC는 기어를 수차에 연결한다.

다. CB (Center Body)

Figure 108 : FRW Center Body 3, 4, 5이다.

날개 수에 따라서 3, 4, 5로 나뉘며, 원형 둘레는 Flap Frame의 각도 제어를 위해 설치하였다.


C : ADW 설명

C-1 : ADW 개략도

Figure 19 : ADW 개략도. ADW 3 Flap StraightFlapWF, ADW 부품 정의

Figure 20 : ADW 축 정의

Figure 21 : ADW Axial Dimension

AB-AT :각도블럭 axial 두께

FC-AT : flap cap 축 방향 두께

G-AT : 기어 축방향두께

LAG-AT: Linear Angle Guide Axial Thickness

BFL: Bar Fix Length

LBT: Linear Bush Thickness

LAG-LB-B-T: LAG linear bearing body thickness

LAG-B-AT: LAG Body Axial thickness


Figure 22 : ADW Radial Dimension. ADW FF에서 Pin-Slot 거리를 기재하였다. (-45~45 변역 기 준)

C-3 : 부품 별 설계

가. ADW FF, ADW Angle Block


Figure 23 ADW FF. FF에 부착되어 각도를 0~90도까지 제어하게 된다. / ADW Angle Block

나. FC


Figure 24 ADW FC, 3, 4, 5. B-ALA (Bar- Angle Linear Axis)를 꽂기 위한 고정 축이 있다.

다. CB


Figure 25 ADW CB 3, 4, 5. FRW와 다르게 원형 받침대 없이 경량이다.

라. LAG


Figure 26 LAG (Linear Angle Guide). 26-A : LAG가 조립된 모습. Angle Block에 연결되어 이동하 면서 동시에 B-FPS에 연결되어 Flap의 각도를 정한다. 26-B : LAG의 모습.

D : Flap 설명


Figure 27 27-A: Straight Flap, 27-B: StraightFlapWF, 27-C: Half Capsule Flap, 27-D: Full Capsule Flap

### B. FRW의 이론적 분석

날개의 각도를 직접적으로 조정하지 않고 날개 각의 회전 각의 범위를 제한하여 자 유롭게 날개가 회전할 수 있도록 설계한 FRW에 작용하는 힘, 토크, 시간에 따른 각 도 등을 분석해보았다.

유체 속에서 운동하는 모델을 단순화하여 분석하기 위해 다음과 같은 가정을 하였다.

### 1. 모든 물 입자의속도 벡터 방향은 동일하다

### 2. 물은 충돌 시 탄성충돌을 한다

3. 물의 유속은 모든 지점에서 동일하다.
4. 모든 날개의 운동은 독립적이다.


Figure 28 FRW 모식도

물의 방향과 i 번째 막대 끝의 각도를 라 하자 ( )

반지름 방향과 i 번째 막대의 방향 사이 각도를 라 하자

다음 성질을 만족한다.

1) 흐르는 물속에서 날개가 받는 힘
날개의 길이 l, 날개의 폭을 w일 때, 날개와 물의 각도 | 는 이다.

물 입자가 날개와 충돌하여 생기는 운동량의 변화를 통해 힘을 구할 수 있다.

2) f, , 의 관계 구하기

원판의 중심을 (0,0)으로 설정하고 벡터로 구분하여 관계를 구할 수 있다.

: 막대가 받는 힘 (원판 - )

: 의 접선 방향 성분 , : t방향 단위 벡터

: 의 반지름 방향 성분, : r방향 단위 벡터

원판 회전운동 방정식 :

i번째 막대 회전운동 방정식 : | ->

i번째 막대 무게중심의 위치 벡터

i번째 막대 중심의 가속도

이므로, i번째 막대에 대한 단위벡터는 회전변환의 형태로 표현된다.

i번째 막대 중심의 가속도 단위 벡터로 표현하기

각각의 단위 벡터에 대해 성분을 비교해보자

### 1. 방향

### 2. 방향

위 두 식을 연립하여 과 을 구할 수 있다.

과 을 원판과 막대의 회전 운동방정식에 대입하면 터빈의 운동을 예측할 수 있다.

### 4. 연구결과

### A. CFD 결과

CFD는 Autodesk CFD 2024를 이용하여 수행했으며, 300 * 300 *300 mm의 큐브에 Flap을 넣어 유속과 이루게 되는 각을 바꾸어 가며 힘을 측정하였다.

각도는 10도 단위로 바꾸어 가며 0~350에 대해서 실험을 수행했으며 벽 계산기를 이용 하여 날개에 가해지는 힘을 구하였다.

큐브의 한쪽 면에는 1m/s의 조건을 주고, 반대편에는 0Pa의 압력 경계조건을 주었다.

다음은 CFD로 도출해낸 각 날개 4 종류 (FullCapsuleFlap, HalfCapsuleFlap, StraightFlap, StraightFlapWF)에 대한 유속단위벡터에 대한 각도에 대한 힘 그래프이다. Fy는 유속에 같은 방향의 힘이며, Fz는 중력에 반대되는 방향의 힘이다. (단위 : N)


Figure 29 : CFD를 통해 구한 유속단위벡터에 대한 각도에 대한 힘 그래프이다.

형상으로 인해 FullCapsuleFlap과 HalfCapsuleFlap의 경우 180도를 기점으로 비대칭적 인 힘이 발생하지만, StraightFlap과 StraightFlapWF의 경우에는 대칭적인 흐름이 만들

어진다. | 이러한 | 대칭성은 | 수차의 | 효율을 | 감소시키는 | 요인이므로,
FullCapsuleFlap/HalfCapsuleFlap과 같이 비대칭적인 힘 그래프에서 더 좋은 성능이 나올 것을 기대할 수 있다.

Wing Fence란 비행기와 같은 항공기에서, 날개의 추력을 증가시키기 위해 날개에 적 용하는 속도방향의 튀어나온 구조물이다. 이러한 WingFence구조를 적용한 것이 StraightFlapWF이다. 하지만 CFD 결과로 비교해 볼 때, Fy의 표준편차는 거의 유사하 며 Fz의 표준편차가 StraightFlap이 더 큰 것으로 유추해 보아 (StraightFlap Fz STDEV 4.3N, StraightFlapWF 3.92N) 이므로 오히려 WingFence 구조를 적용한 구조물에서 효 율이 감소함을 알 수 있다. 이는 공기에 비해 물의 높은 점성으로 인한 손실에서 기 인한다고 판단된다.

### B. ADW의 성능 최적화, 예측

B-1 ADW 최적화 과정

ADW에서, 날개의 각도는 모든 theta에 대해 phi의 값을 정해줌으로서 최적화가 가 능하다. 이때 날개의 phi의 값을 정하는 것은 Angle Block의 radial length에 의해 결 정되는 것이다.

날개와 유속벡터가 이루는 각을 delta로 두면, theta와 phi, delta의 관계를 유도할 수 있다. ADW 성능 최적화를 위해 optimizer 코드를 구성하였다. Optimizer 코드는 CFD 분석을 통해 얻은 힘 데이터를 이용하여 날개 형상에 최적화된 Angle Block의 형상 을 정해주는 코드이다.

모든 theta에 대해서, phi의 각도 범위 0~90에 대해 delta의 범위가 정해지며, 해당 범위 내에서 최대의 토크를 나타내는 phi의 값을 지정한다. 토크는 모멘트암 * 힘이 라는 간단한 공식을 이용하여 구하였으며 이는 Figure 23에 나오는 코드를 통해 구 한다.


Figure 30: torque code

최대 토크를 위 코드로 맵핑 한 이후, 이 theta와 phi의 관계를 나타내는 리스트를 thetaphi_raw로 저장한다. 해당 리스트를 바로 AngleBlock의 형상으로 바꿀 수 있으 면 좋겠지만 과도한 기울기로 인한 저항을 고려하기 위해 Smoothing 절차를 추가 하였다.

Smoothing 절차는 값을 더 원만하게 만들기 위해서 사용하는 절차로, 다음과 같이 작동한다. 모든 요소를 자기 앞과 뒤를 포함한 3 요소의 평균값으로 업데이트한다. 이를 재귀적으로 k번 반복하는 것이 아래 Figure 23-B의 smoothout 함수이며, 구현 가능한 형태의 AngleBlock을 만드는데 필수적이다.


Figure 31 : A : phitor, B : smoothing 코드

AngleBlock은 Phi값이 아닌 radial 값으로 맵핑되기 때문에 phi to r 코드를 이용해 서 radial값으로 바뀌어야 한다. 이러한 함수를 통해 phitor로 변환된 이후, radial 정 보를 이용하여 점을 찍어 Dxf (출력 가능한 스케치 파일 형태) 로 변환 이후 AngleBlock으로 만들 수 있다.

Smoothing을 통해 Phi Distribution ( Theta 와 Phi 사이 관계 리스트)가 바뀌면, 이 를 통해 얻어지는 최대 성능 또한 바뀐다. 이러한 성능 저하를 측정하기 위해 Phi Distribution에서 얻어지는 전체 Torque를 계산하는 코드를 구현하였다.

다음은 그 코드로 구해진, smoothing으로 인한 성능 저하이다.

Smoothing을 재귀적으로 3, 5, 10번 적용 한 것의 손실을 나타낸 것이다. 이때 최대 토크는 HalfCapsuleFlap-FullCapsuleFlap-StraightFlap-StraightFlapWF 순서로 좋다는 것을 알 수 있다.

Figure 32: Total Torque of Optimized Rotor

이때 단순한 Repeated Mean 방식이 아닌 다른 방식으로 Smoothing을 구현하면 더 높은 효율과 낮은 저항을 얻을 수 있을 것이라고 생각한다.

### C. 일반적인 물레방아와 효율 비교

일반적인 물레방아를 개선한 우리의 수차의 토크 예상치가 일반적인 물레방아에 비 하여 더 높은 토크를 얻을 수 있는지 구해보았다. 날개 사이에 유체의 간섭은 없다 고 가정하였으며, 날개가 단일하게 존재할 때 받는 힘이랑 물레방아 안에서 받는 힘 이 같다고 가정하였으며, 물레방아의 날개는 모두 phi = 90이며 물에 담긴 영역은 theta 180~360도로 두고 토크를 계산하였다.


Figure 33 : Raw Flap & SmoothFlap 물레방아 비교 성능 향상

Raw하게 맵핑한 경우, FullCapsuleFlap에서 40%의 성능 향상, HalfCapsuleFlap에서 24% 의 성능향상이 있을 것으로 기대되었으며, StraightFlap과 StraightFlapWF은 18%, 22% 의 성능향상이 있을 것으로 기대되었다. Smooth3의 경우 성능이 많이 저하되어 FullCapsule와 HalfCapsule에서 약 12%의 성능향상이 있을 것으로 기대되었다.

### 5. 결론

### A. 고찰

FRW의 경우 어항의 설계 오류로 인해 실험을 제대로 진행하지 못했다. 하지만 FRW는 회전하는 데에 수력을 소모하기 때문에 일반적인 물레방아에 비교하여 높은 효율을 얻기 는 힘들 것으로 예상된다. FRW의 회전이 이루어지는 과정은 관찰하였지만 이것이 유의 미한 실험 결과로 이어지지는 못했다.

물리 이론적인 분석을 통해서 미분방정식을 유도해내었지만 이 또한 컴퓨터로 풀리는 형 태가 아니어서 무척이나 물리적으로 복잡한 계를 다룬다는 것을 알았으며 이러한 접근 방식으로 FRW를 개발하기는 무척 어렵다는 것을 깨달았다.

ADW의 경우, CFD를 통해 얻은 데이터를 바탕으로 유의미한 최적화가 가능했다. ADW를 이용하여 물레방아에 비교하여 효율을 40% 가까이 증가시킬 수 있음을 확인하였으며, 강의 수심을 2배 가까이 활용할 수 있다는 것을 알아냈다. 프로펠러에 비해 대형화하기 쉬운 구조로, 특정 부품 (Angle Block, LAG)의 내구도 문제가 해결되면 유용한 해결책일 것으로 예상된다. 하지만 회전체의 지나치게 복잡한 구조로 인해 빠른 유속에서는 적용 불가능 할 것으로 예상되며 느린 유속에서 최대 효율을 이끌어내는데 좋은 해결책일 것 으로 예상된다.

### B. 결론

강과 같은 광폭 저속 수로에서 발전가능한 접이식 수차를 개발하기 위해 FRW와 ADW의 두 가지 아이디어를 내었다. 이러한 아이디어를 검증해 보았을 때, FRW의 경우 기존 물 레방아에 비해 낮은 효율을 가진다는 것을, ADW의 경우 최대 40%의 높은 효율을 성취 해 낼 수 있음을 알아내었다. 하지만 이 과정 또한 수많은 가정이 들어가 있는 결론으로, 어항을 개선하여 실제 환경에서 실험을 진행하여야 유의미한 결론을 얻을 수 있을 것으 로 생각된다.

### C. 제언

### 1. FF 부품의 내구도 문제

수많은 Flap 구조를 효율적으로 실험하기 위해, 수차의 날개를 부품 수 총 3개로 조립식 으로 구성하고자 하였다. 이 과정 속에서 3D 프린터와 아크릴을 혼용해서 사용하였으며, 날개와 같이 견고해야 하는 부품이 과도하게 복잡한 형상으로 설계되어 내구도에 문제가 생겼다. FF 부품은 자꾸 부러졌으며 3D 프린터로 뽑은 부품은 설계 공차를 고려하지 않 고 오차로 인해 폭이 5mm보다 좁은 문제가 생겼다.

실제 발전소에 적용시에는 이러한 문제가 없도록 날개를 일체형으로 설계해야 할 것이 다.

FF 부품은 일체형 레진으로 수정하여 2차 보완 실험을 진행할 것이다. 내구도에 대한 우 려가 훨씬 적어질 것으로 기대된다.

### 2. 어항의 설계 문제

어항 내부에서 물을 순환시키기에 역부족인 설계를 하였으며 이에 대한 검증이 부족하 였다. 모터로 추진된 물은 벽면에 맞아 원하는 대로 회전하지 않았으며, 벽에 맞은 이후 상승하여 역행하는 현상을 일으켜 상류와 하류에 반대되는 물의 흐름이 일어났다. 이러 한 문제로 인해 수차의 회전 실험이 제대로 진행되지 못했다. 하지만 물이 예상대로 흐 르는 경우, CFD 결과를 이용해 유의미한 예측을 할 수 있다. 차후에 어항의 물 순환을 바꾸어 다시 진행해볼 계획이다. 어항 모터를 하나 더 추가해서 흐름을 제어하며, 아크릴 로 물의 경로를 제어하여 다시 시도할 것이다.

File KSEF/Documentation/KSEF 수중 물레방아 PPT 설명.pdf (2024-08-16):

# 연구발표자료 - 1


한화 사이언스 챌린지에서는, 새로운 아이디어를 제안하고 그 아이디어를 실제로 구현하는 과정에 중점을 두었습니다. 이를 통해 구현 가능한 아이디어임을 확인하였습니다. 반면, KSEF에 출전할 때에는, 아이디어의 효율성을 높이고, 그 성능을 실질적으로 검증하는 데 초점을 맞췄습니다.


프로토타입 (좌측 이미지):
- 실험을 위해 제작한 초기 프로토타입은 자석 간의 척력을 이용해 마찰을 최소화 시킨 Angleblock인 자기부상 Angleblock을 사용했으며, 날개의 크기가 작았습니다. 하지만 자기부상 Angleblock의 구조적 문제와 작은 날개 크기로 인해 프로토타입은 회전하지 않았습니다.
3-Flat Version (우측 이미지):
- 이를 개선하기 위해, 첫 번째로, 날개의 크기를 증가시켰습니다. 더 큰 날개는 더 많은 물을 받아 더 큰 토크로 회전하게 됩니다.
- 두 번째로, 모델링 변화를 통해 구조를 경량화하였습니다. 자기부상 Angleblock 대신 기존의 베어링 Angleblock을 사용하였으며, 날개 전체를 3D 프린터로 출력하는 대신 뼈대만 3D 프린터로 출력하고 셀로판지를 붙여 경량화했습니다.
- 세 번째로, 30X30 알루미늄 프로파일로 실험대를 제작해 기존의 탄소섬유
봉으로 | 만든 | 실험대에 비해 실험대의 안정성을 향상시키고 | 비틀림을
감소시켰습니다.

결론: 이러한 개선점들을 통해 3-Flat Version은 초기 프로토타입에 비해 월등히 잘 회전하였으며, 발전 가능성을 보여주었습니다.


3-Flat Version (좌측 이미지):
- 초기 모델인 3-Flat Version에서는 날개 3개를 사용하였습니다. 이 모델을 통해 기본적인 설계를 확인하고 초기 실험을 진행하였습니다.
4-Flat Version (중앙 이미지):
- 3-Flat Version에서 얻은 데이터를 바탕으로, 날개 개수를 3개에서 4개로 늘렸습니다. 구조적으로 가능한 최대 날개 수는 4개였으며, 회전 시 수차가 정지하지 않고 회전하기 위해 날개 수를 4개로 늘렸습니다.
4-Curved Version (우측 이미지):
- 날개 개수 증가뿐만 아니라 날개의 형태도 반원 형태로 변경하여 성능을 비교했습니다. 반원 형태의 날개는 물의 저항을 줄이고 더 큰 발전량을 얻기 위해 설계되었습니다.


왼쪽 이미지의 Endless Pool은 일정한 물의 흐름을 제공하여 다양한 수중 실험을 진행할 수 있는 시설입니다. 저희는 돈을 모아 풀을 대여하여 유속 변화에 따른 수차의 회전 속도를 측정하는 실험을 수행하였습니다. Endless Pool은 큰 유속 균일성과 정밀한 유속 제어가 가능해 유속에 대한 변수를 실험할 수 있었지만, 추를 매달아 발전량을 측정할 수는 없었습니다.

오른쪽 이미지의 테스트 베드는 이 프로젝트를 위해 선재가 학교 내에 직접 제작한 실험 환경입니다. 1000L 물탱크 3개로 구성되어 있으며, 유속을 조절할 수 없어서 일정한 유속으로 물이 흘렀습니다. 이 점을 활용하여 학교 테스트 베드에서는 일정한 유속에서, 추의 무게로 수차에 걸리는 부하를 바꾸어가며 발전량 실험을 했습니다.

이 두 실험 환경을 통해 저희는 각각 유속과 부하를 바꾸어가며 유의미한 성능 측정을 할 수 있었습니다.


저희는 Endless Pool에서 실험한 데이터를 바탕으로 외부 유속에 따른 평균 각속도의 변화를 분석했습니다. 그래프에는 두 가지 형태의 날개, 곡선형(Curved)과 평면형(Flat)의 성능 차이가 비교되어 있습니다.

그래프의 X축은 외부 유속 (m/s)을 나타내고, Y축은 평균 각속도 (rad/s)를 나타냅니다. 두 종류의 날개가 각각 파란색 (Curved)과 빨간색 (Flat) 선으로 표시되어 있습니다.

외부 유속이 증가함에 따라 두 종류의 날개 모두 평균 각속도가 증가하지만, 곡선형 날개가 평면형 날개보다 모든 구간에서 더 높은 각속도를 보입니다. 따라서 곡선형 날개가 평면형 날개에 비해 더 효율적으로 설계되었음을 알 수 있습니다. 이와 같은 분석을 통해 저희는 곡선형 날개의 설계가 수차의 성능을 향상시킬 수 있는 중요한 요소임을 확인할 수 있었습니다.

# 연구자료발표 – 6


저희는 다양한 부하 조건에서의 성능을 비교하기 위해 위의 발전량 실험을 설계하였습니다. 발전량은 수차가 반지름이 7mm인 풀리에 매달린 추에 하는 일률을 기준으로 측정하였으며, 그래프의 X축은 평균 각속도(rad/s)를 나타내고, Y축은 발전량(W)을 나타냅니다.

부하가 증가함에 따라 평균 각속도는 감소하지만, 일정 부하(800g) 조건에서 최대 발전량을 기록하는 것을 확인할 수 있었습니다.

이와 같은 분석을 통해 최적의 부하 조건을 찾는 것이 중요하며, 800g의 부하 조건이 곡선형 날개의 효율을 극대화할 수 있는 적절한 조건임을 확인할 수 있었습니다.

# 연구발표자료 – 7


기존의 베어링 Angleblock에서는 베어링과 Anglelblock가 서로 맞물려 회전하기 때문에, 마찰로 인한 손실과 Angleblock과 베어링의 마모가 발생합니다. 이러한 문제를 해결하기 위해 제가 자기부상 Angleblock 아이디어를 제안하여 만들어보게 되었습니다.

하지만, LAG (Linear Axis Guide, 왼쪽 이미지에서 Angleblock에 맞물려 회전한다) 회전 중 Angleblock의 자석과 LAG의 자석이 서로 붙는 문제가 발생했습니다. 이는 막대 자석을 여러 개 꽂아 곡면 구조를 만들려고 했기에 발생한 문제입니다. 이를 해결하기 위해서는 강자성체로 막대 자석들의 자기장을 부드럽게 만들거나, 별도의 원형 자석을 만들어야 합니다.

왼쪽 이미지는 자기부상 Angle Block과 LAG의 상호작용을 보여줍니다.
오른쪽 이미지는 자기부상 Angleblock의 제작 사진입니다. 저희는 자석의 종류, 간격, 두께, 3D 프린팅 구조물로 감싼 여부를 바꾸어가며 엄청나게 많은 시도를 했지만 모두 실패했습니다.

# 연구발표자료 – 8


저희 수차를 실제 발전 환경에 적용하였을 때, 예상되는 효과는 다음과 같습니다. 강에서의 적용:
- 녹조 제거 효과: 제안된 시스템은 강에서 녹조를 제거하는 데 도움이 될 수 있습니다.
- 배 이동 가능: 시스템 설치가 배의 이동에 방해가 되지 않도록 설계되었습니다.
- 어류 보호: 느린 유속에서 천천히 큰 토크로 회전하기 때문에 어류를 보호할 수 있습니다.
시스템 설치 및 발전량:
- 저희가 제안한 수차는, 수차가 유체 속도와 수직한 축으로 회전하며, 회전 원리가 유사하다는 점에서 VAWT(Vertical Axis Wind Turbine)와 유사합니다. 따라서, 저희가 제안한 수차의 발전량은 VAWT 의 발전량이 유속의 세제곱에 비례하며, 단면적에 비례한다는 사실을 기반으로 계산했습니다. 이러한 원리를 저희 수차에도 근사적으로 적용하여 예상 발전량을 산출하였습니다.
- 제안된 시스템을 한강에 설치할 경우, 10m 깊이에서 1200m의 간격으로 설치하여 총 6.48MW의 발전량을 확보할 수 있습니다.
결론:
- 저희 연구는 청정하고 강력한 에너지 수확 방법을 제안하며, 이는 환경을 보호하고 지속 가능한 에너지 생산을 가능하게 합니다.

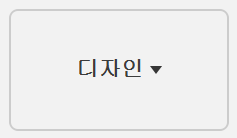
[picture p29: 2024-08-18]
HSC2023 한화 사이언스 챌린지/Analysis Data and Code/Code and DXF/CFD automation/designbutton.png

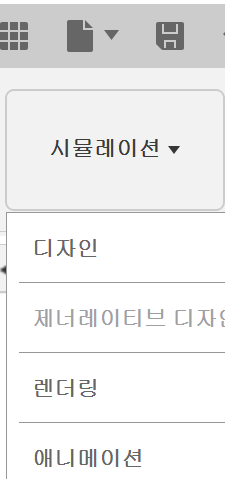
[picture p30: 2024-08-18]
HSC2023 한화 사이언스 챌린지/Analysis Data and Code/Code and DXF/CFD automation/designbuttonsmall.png

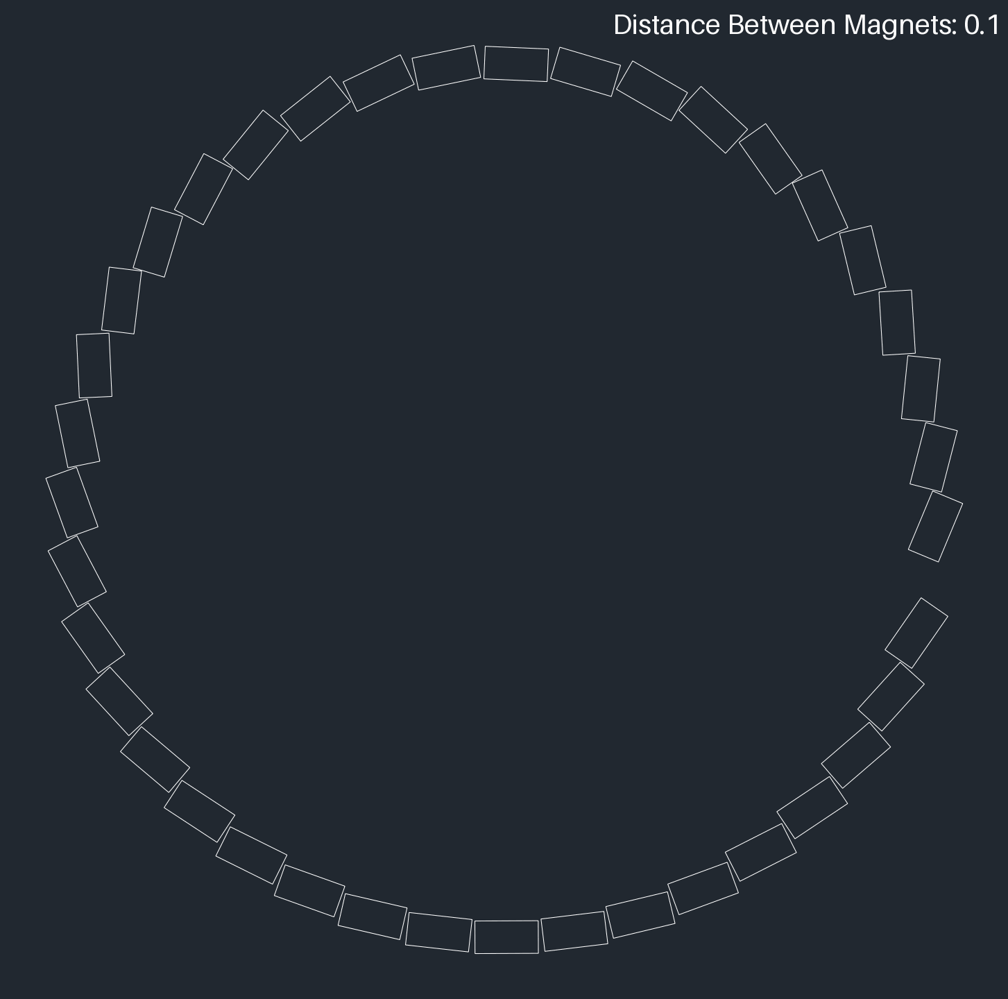
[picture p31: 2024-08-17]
KSEF/Code Analysis/DXF_V3/IMG/V3_outer.gif

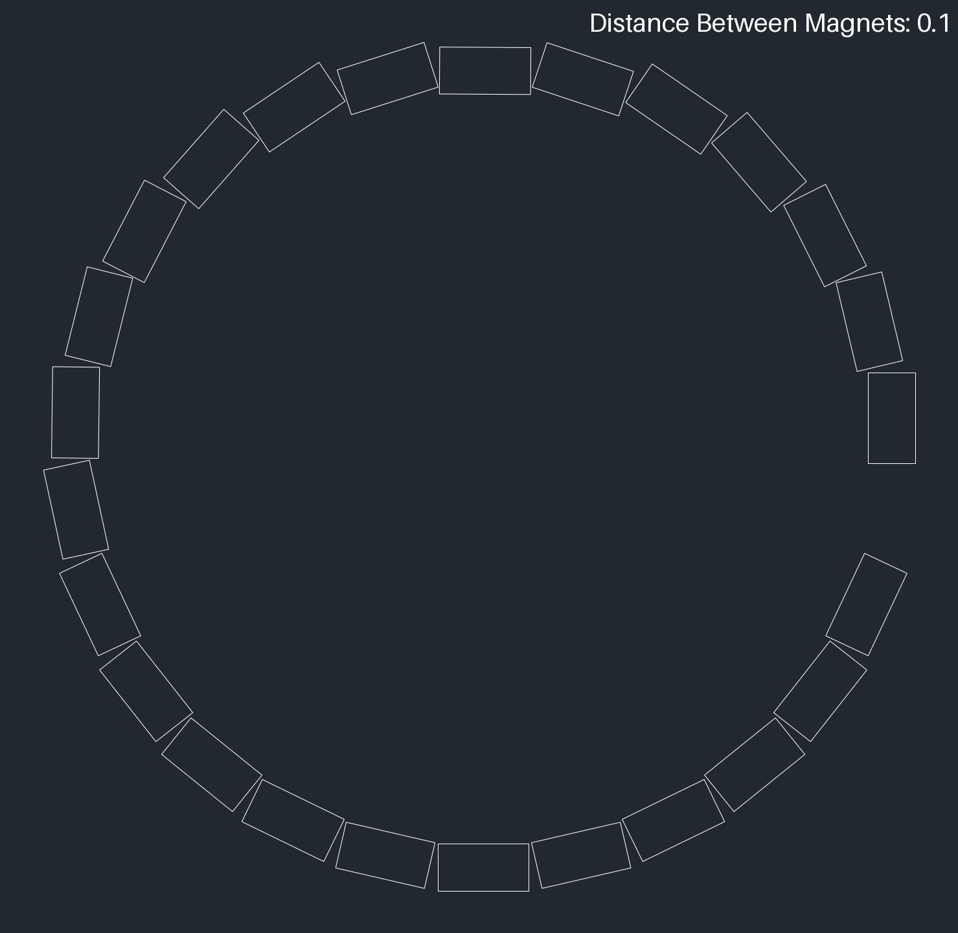
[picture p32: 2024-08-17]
KSEF/Code Analysis/DXF_V3/IMG/V2_inner.gif

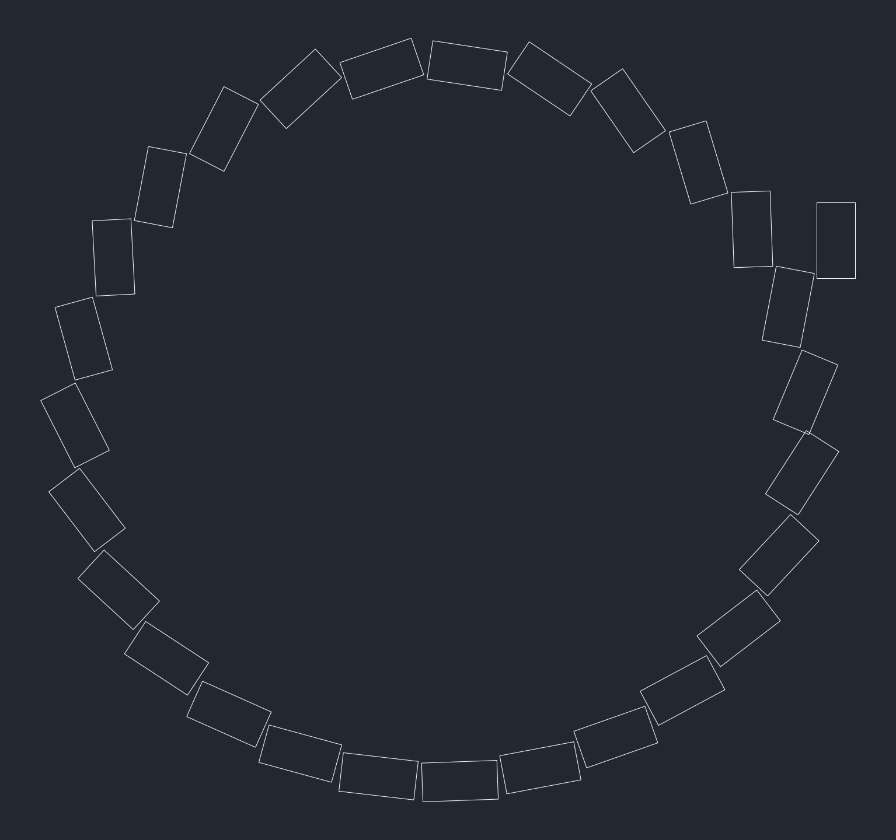
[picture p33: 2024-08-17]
KSEF/Code Analysis/DXF_V3/IMG/inner0.3500000000000001.png

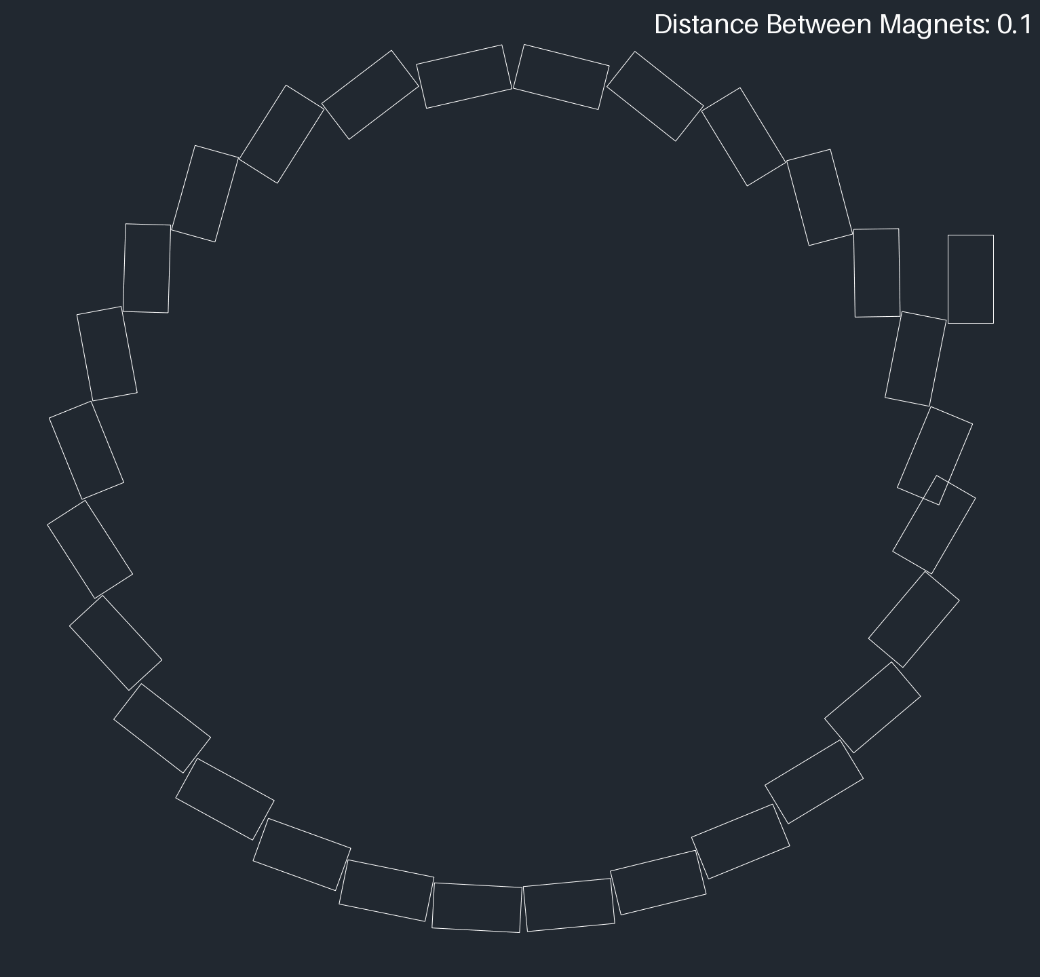
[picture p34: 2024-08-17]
KSEF/Code Analysis/DXF_V3/IMG/V3_inner.gif

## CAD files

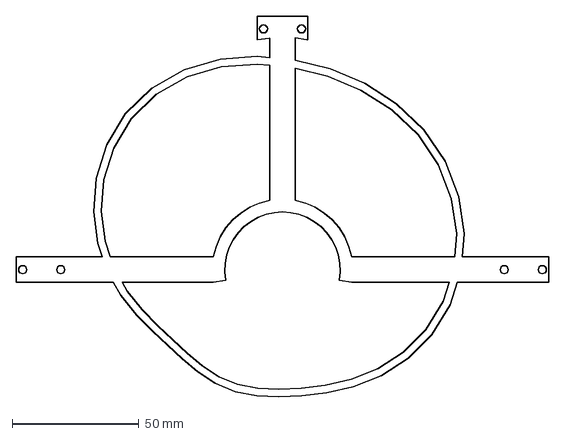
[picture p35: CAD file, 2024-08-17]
HSC2023 한화 사이언스 챌린지/Analysis Data and Code/Code and DXF/fullcap/fullcapmount.dxf
210.0 x 150.2 mm

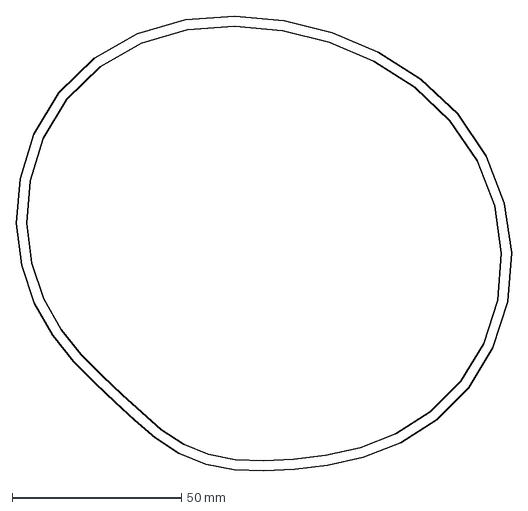
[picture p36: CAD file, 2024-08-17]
HSC2023 한화 사이언스 챌린지/Analysis Data and Code/Code and DXF/fullcap/fullcap.dxf
146.2 x 134.3 mm

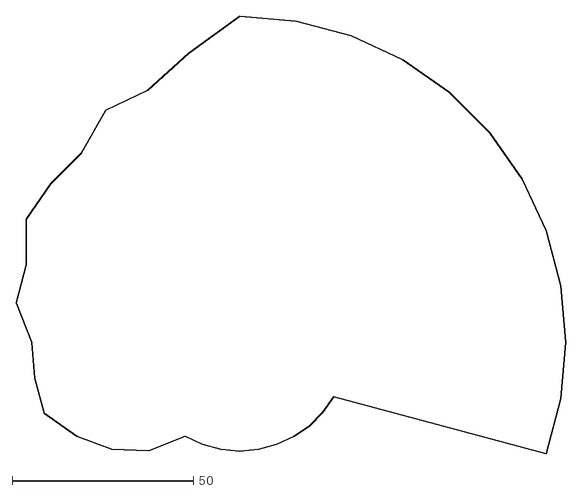
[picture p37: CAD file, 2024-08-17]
HSC2023 한화 사이언스 챌린지/Analysis Data and Code/Code and DXF/halfcap/raw.dxf
151.7 x 120.8

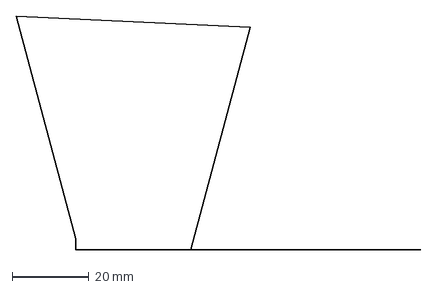
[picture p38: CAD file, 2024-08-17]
HSC2023 한화 사이언스 챌린지/Analysis Data and Code/Code and DXF/spreader.dxf
105.5 x 60.9 mm

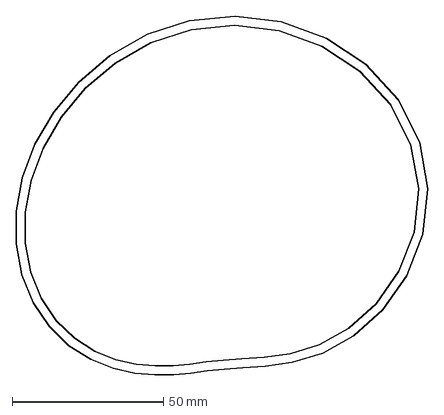
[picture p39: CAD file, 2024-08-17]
HSC2023 한화 사이언스 챌린지/Analysis Data and Code/Code and DXF/straightflap/straight.dxf
136.0 x 118.6 mm

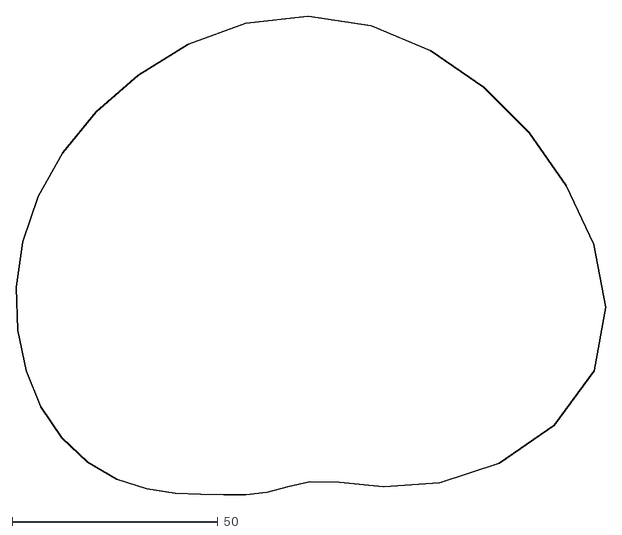
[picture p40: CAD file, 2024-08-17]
HSC2023 한화 사이언스 챌린지/Analysis Data and Code/Code and DXF/straightflapWF/sm3.dxf
143.3 x 116.4

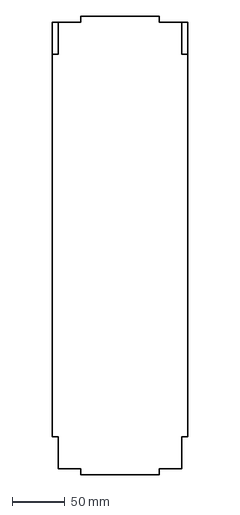
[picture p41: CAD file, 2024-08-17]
HSC2023 한화 사이언스 챌린지/설계/Acryl Wall Dxf.dxf
129.0 x 436.0 mm

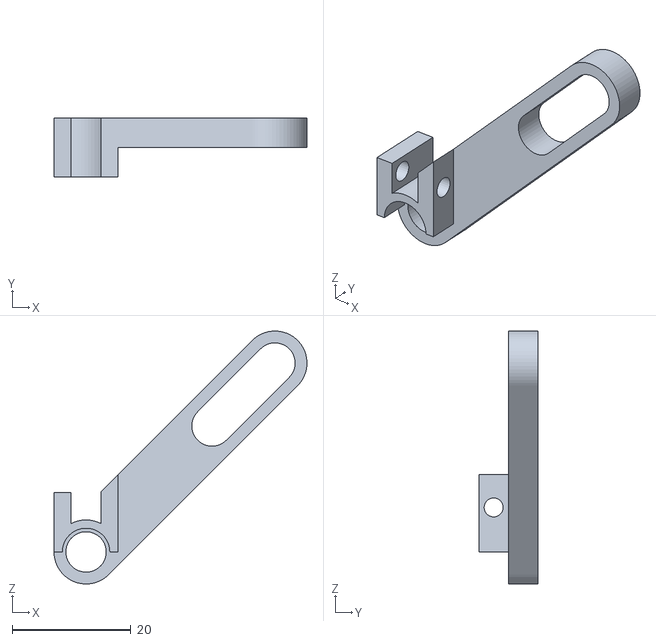
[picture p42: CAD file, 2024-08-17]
HSC2023 한화 사이언스 챌린지/설계/STL/ADW/ADW FF L.stl
42.6 x 10.0 x 42.6

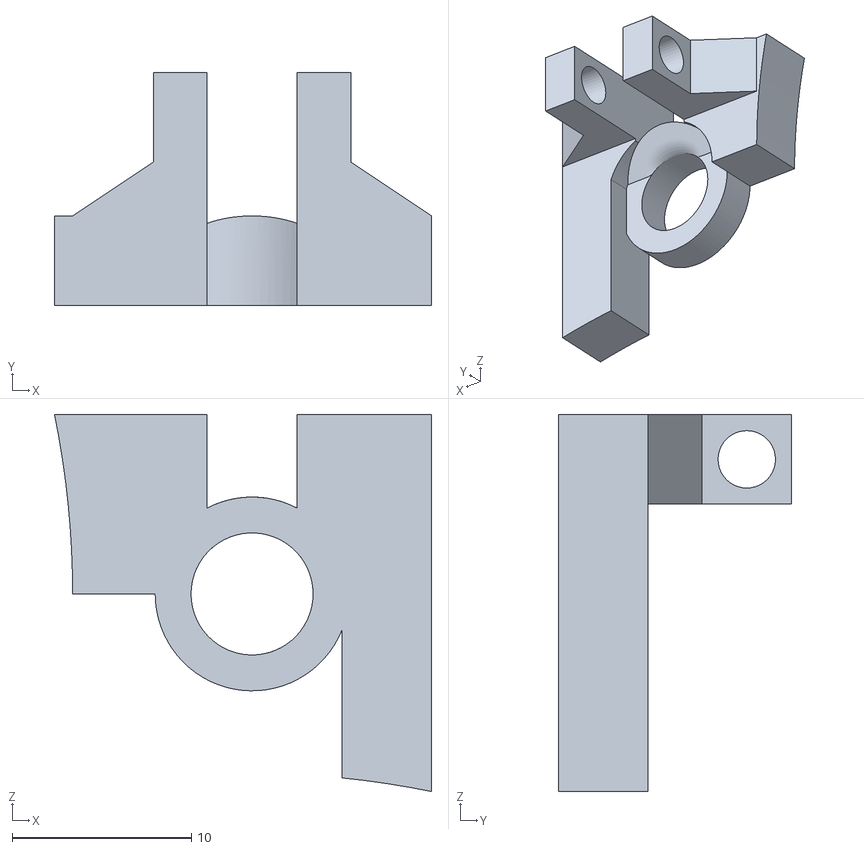
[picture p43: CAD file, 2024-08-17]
HSC2023 한화 사이언스 챌린지/설계/STL/all/FRW FF 0-90 L.stl
21.0 x 13.0 x 21.0

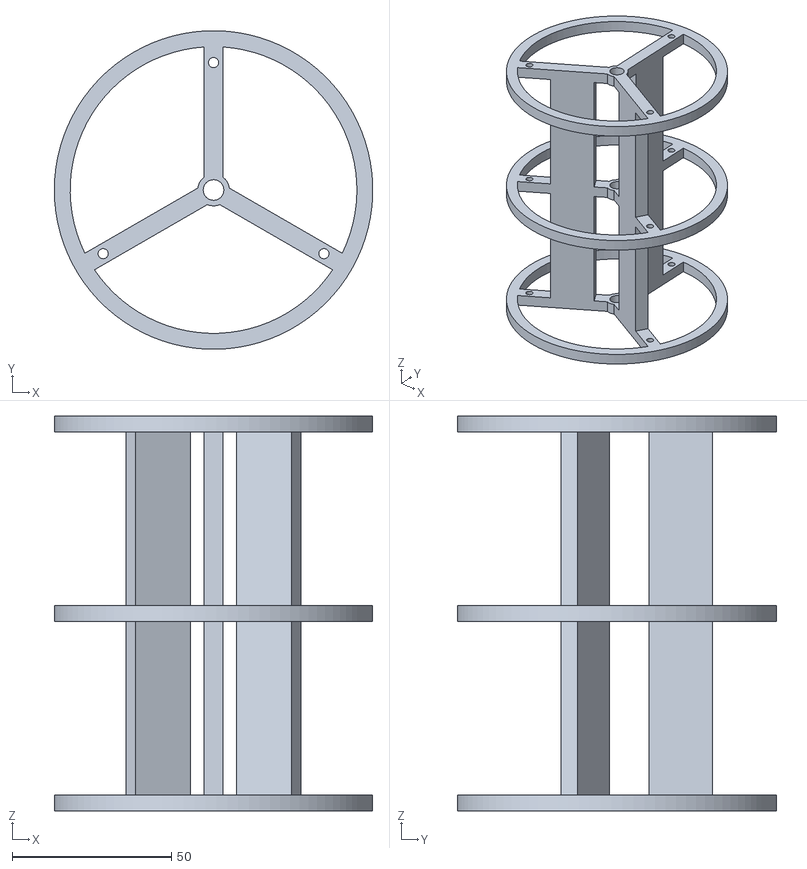
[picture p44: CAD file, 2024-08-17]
HSC2023 한화 사이언스 챌린지/설계/STL/FRW/FRW CB 3.stl
100.0 x 100.0 x 124.0

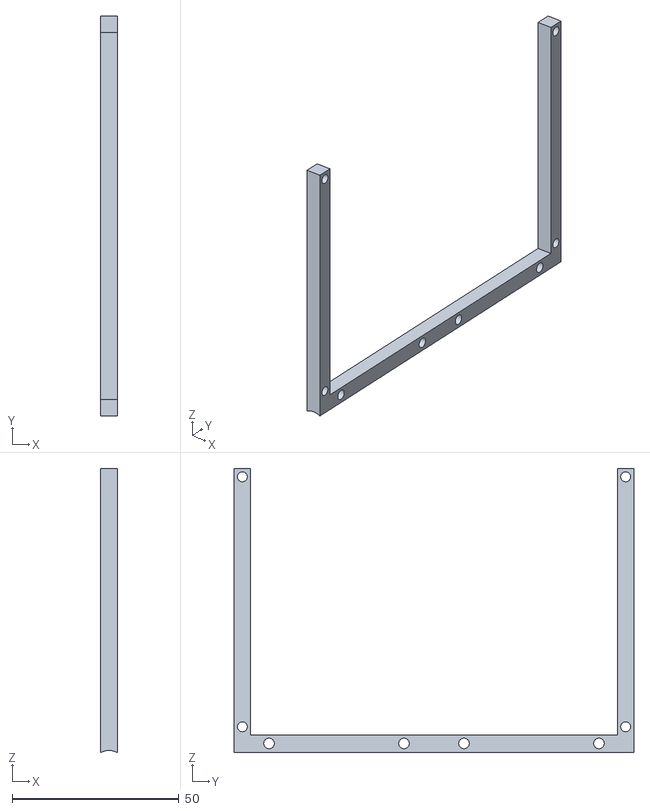
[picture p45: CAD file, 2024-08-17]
HSC2023 한화 사이언스 챌린지/설계/STL/공통/FF.stl
5.00 x 120.0 x 85.2

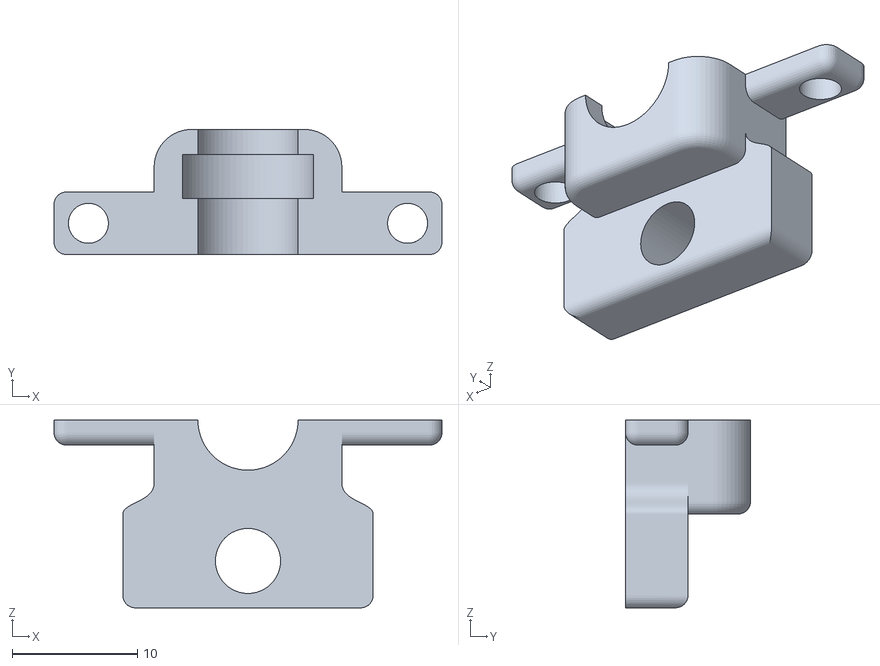
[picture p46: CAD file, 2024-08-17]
HSC2023 한화 사이언스 챌린지/설계/어항 설계/stls/barmount0 (upper).stl
31.0 x 10.0 x 15.0

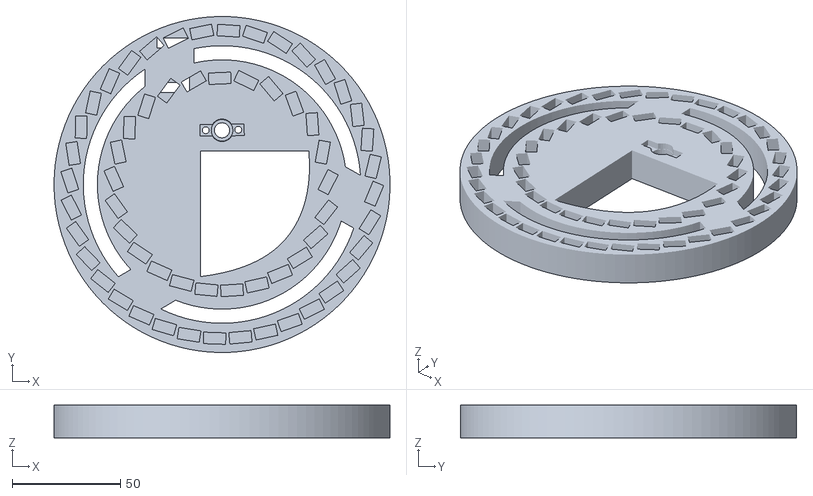
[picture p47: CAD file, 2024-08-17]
KSEF/BUILD/경량 노출 자석 버전/Angleblock 경량 노출 자석 버전/경량 자석 Angleblock 3mm/A.stl
155.0 x 155.0 x 15.0

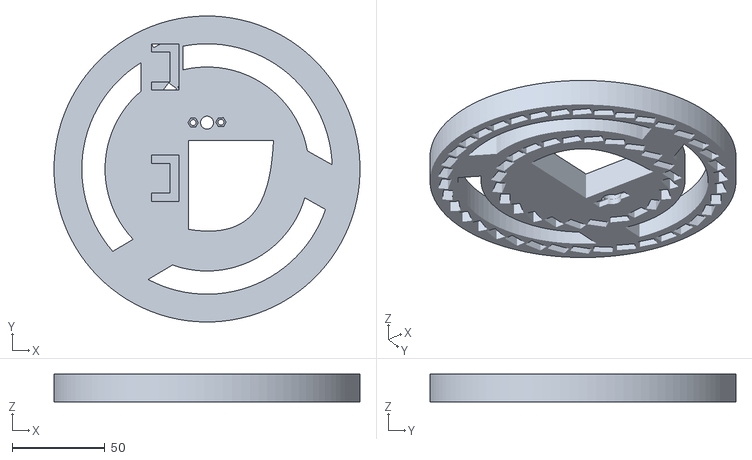
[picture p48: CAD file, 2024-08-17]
KSEF/BUILD/경량 노출 자석 버전/Angleblock 경량 노출 자석 버전/경량 자석 Angleblock 5mm/B.stl
165.0 x 165.0 x 15.0

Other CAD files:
KSEF/BUILD/경량 노출 자석 버전/Angleblock 경량 노출 자석 버전/경량 자석 Angleblock 8mm/AB 8mm outer.dxf
KSEF/BUILD/베어링 버전/Angleblock 베어링 버전/3030HolderAB.stl
KSEF/BUILD/베어링 버전/Centerbody V5 LW.stl
KSEF/Code Analysis/DXF_V3/dxfs/outer0.35.dxf
HSC2023 한화 사이언스 챌린지/Analysis Data and Code/Code and DXF/abmount.dxf
HSC2023 한화 사이언스 챌린지/Analysis Data and Code/Code and DXF/fullcap/raw.dxf
HSC2023 한화 사이언스 챌린지/Analysis Data and Code/Code and DXF/fullcap/sm10.dxf
HSC2023 한화 사이언스 챌린지/Analysis Data and Code/Code and DXF/fullcap/sm3.dxf
HSC2023 한화 사이언스 챌린지/Analysis Data and Code/Code and DXF/fullcap/sm5.dxf
HSC2023 한화 사이언스 챌린지/Analysis Data and Code/Code and DXF/halfcap/halfcap.dxf
HSC2023 한화 사이언스 챌린지/Analysis Data and Code/Code and DXF/halfcap/halfcapmount.dxf
HSC2023 한화 사이언스 챌린지/Analysis Data and Code/Code and DXF/halfcap/sm10.dxf
HSC2023 한화 사이언스 챌린지/Analysis Data and Code/Code and DXF/halfcap/sm3.dxf
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

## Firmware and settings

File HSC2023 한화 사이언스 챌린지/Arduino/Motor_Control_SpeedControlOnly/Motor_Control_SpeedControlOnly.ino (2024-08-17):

#include <Wire.h>
#include <Servo.h>

Servo ESC;

const int escpin = 9;

const int upbuttonpin = 5;
const int downbuttonpin = 6;
const int ledpin = 13;

int power = 0; 
int waterspeed = 0;

void servobyms(int ms){
  ESC.write(map(ms, 1, 2, 0, 180));
}

void initesc () {
  // (1) connect the esc ground -> by switching on, it turns on
  // give esc 1ms or 2ms which means maximum speed
  servobyms(1);
  delay(1000);
  //give esc neutral signal
  servobyms(1.5);
  delay(1000);
  //initial end
}


void setup() {
  ESC.attach(9);  // 서보를 9번 핀에 연결
  initesc();

  pinMode(upbuttonpin, INPUT);
  pinMode(downbuttonpin, INPUT);
  pinMode(ledpin, OUTPUT);
  
  
  Serial.begin(9600);
}

void loop() {
  bool up = digitalRead(upbuttonpin);
  bool down  = digitalRead(downbuttonpin);
  
  int angle = map(power, 0, 100, 90, 0);  // 0~1023 범위를 0~180 범위로 매핑
  
  digitalWrite(ledpin, LOW);
  if (up && power <= 100) power += 1;
  if (down && power >=0) power -=1;
  
  
  ESC.write(angle);  // 서보 각도 제어
  
  Serial.print(up);
  Serial.print("\t");
  Serial.print(down);
  Serial.print("\t");
  Serial.print(angle);
  Serial.print("\t");
  Serial.println(power);

  delay(100);  // 갱신 속도 제어를 위한 지연
}

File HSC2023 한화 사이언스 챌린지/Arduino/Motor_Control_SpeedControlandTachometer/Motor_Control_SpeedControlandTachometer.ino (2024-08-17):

#include <Wire.h>
#include <Servo.h>

Servo ESC;

int speed = 1; // meter/second

float rotor_rev=0.0;
int rotor_rpm;

float water_rev=0.0;
int water_rpm;
float water_rotorradius = 10; // in centimeters
float water_speed;

int oldtime=0;
int time;

bool CW = true;
int pulsew = 1000; // CW false -> 1500 

int ESC_pin = 9;
int rotor_pin = 18;
int water_pin = 19; // on board mega


void calcspeed(){ //changes water_rpm into m/s of water
  float pi = 3.14;
  float metertocm = 100;

  water_speed = water_rpm * water_rotorradius / metertocm * 2 * pi / 60;
}

void adjustESC(){
  if (waterspeed <= speed) {
    pulsew += 5;
  }
  else if (waterspeed >= speed){
    pulsew -= 5;
  }
}


void rotor_isr() //interrupt service routine
{
  rotor_rev++;
}

void water_isr() //interrupt service routine
{
  water_rev++;
}


void setup() {
  ESC.attach(9);  // ESC를 9번 핀에 연결
  Serial.begin(9600);

  attachInterrupt(digitalPinToInterrupt(rotor_pin) ,rotor_isr,RISING); 
  attachInterrupt(digitalPinToInterrupt(water_pin) ,water_isr,RISING);
}

void loop() {
  //indrek's arduspreadsheet , seperated by /t
  delay(1000);
  noInterrupts();
  time=millis()-oldtime;        //finds the time 
  rotor_rpm = (rotor_rev/time)*60000; 
  water_rpm=(water_rev/time)*60000;         //calculates rpm
  calcspeed();
  adjustESC();

  /*

  
  */
  Serial.println(rotor_rpm);
  Serial.println(water_speed);
  Serial.println(speed);

  Serial.print("/t");

  oldtime=millis();             //saves the current time
  rotor_rev=0;
  water_rev = 0;  
  interrupts();
}

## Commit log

2024-08-16 KSEF 2023 저유속 수차 연구.pdf
2024-08-17 HSC2023+KSEF 정리
    [2차 예선 모델링_ADW.f3z, 3030HolderAB.stl, A.stl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]
2024-08-18 CFD automation 추가
